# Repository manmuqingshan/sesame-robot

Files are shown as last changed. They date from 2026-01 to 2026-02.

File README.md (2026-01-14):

# The Sesame Robot Project 
___







sesame-cover

___

**Greetings, from your new best friend.**

Sesame is an accessible Open-Source robotics project based on the ESP32 microcontroller system, with an emphasis on expression and movement. 
This project is designed for makers and engineers of all skill levels! Sesame offers a dynamic platform designed to start working with walking robots. 
To build a sesame robot, you will need basic soldering skills, $50-60 in hardware components, access to a 3D printer, and a basic understanding of Arduino IDE.

This repository contains the CAD design files, STL files, build and wiring guides, and the base/expanded firmware for the ESP32-based controller. 
There is also some included debugging firmware that may be helpful in getting your Sesame up and running.

## Features

*   **Quadruped Design:** Uses 8 servo motors (2 per leg) to achieve roughly 8 total degrees of freedom.
*   **Emotive Display:** Features a 128x64 OLED screen acting as a reactive face that syncs with movement.
*   **Fully Printable:** Designed entirely for 3D printing in PLA with minimal supports.
*   **Sesame Studio:** New animation composer software to easily create custom movements.
*   **Serial CLI:** Control the robot and trigger animations via a Serial Command Line Interface or the web UI.
*   **Pre-programmed Emotes:** Includes animations for Walking, Waving, Dancing, Pointing, Resting, and more.

## Watch the launch video on YouTube

<a href="https://www.youtube.com/watch?v=1UDsWkcQZhc">thumb-youtube</a>

## Getting Started

Follow these steps to build your own Sesame Robot:

### 1. Gather Parts 
Check the **[Bill of Materials (BOM)](hardware/bom/README.md)** for a complete list of required electronics and hardware.
*   Microcontroller: ESP32 S2 Mini
*   Actuators: 8x MG90 Servos
*   Power: 5V 3A source

### 2. Print Parts 
Download the STLs and follow the **[Printing Guide](hardware/printing/README.md)**.
*   Designed for PLA
*   Minimal supports required

### 3. Build & Wire 
Follow the **[Build Guide](docs/build-guide/README.md)** and **[Wiring Guide](docs/wiring-guide/README.md)** to assemble the frame and connect the electronics.

### 4. Flash Firmware 
Upload the code from the **[Firmware Directory](firmware/README.md)**.
*   Requires Arduino IDE
*   Configure WiFi AP settings

### 5. Create Animations 
Use **[Sesame Studio](software/sesame-studio/README.md)** to visually design poses and sequences for your robot.

---

## Software & Firmware

### Sesame Studio
Sesame Studio is a standalone desktop application included in `software/sesame-studio/`. It allows you to:
*   Visually pose the robot using a schematic interface.
*   Generate C++ code for servo angles automatically.
*   Sequence frames into complex animations.

[**> Go to Sesame Studio**](software/sesame-studio/README.md)

sesamestudio-preview

### Firmware
The ESP32 firmware handles the kinematics, face display, and WiFi control interface.
*   **Web UI:** Control the robot from your phone via the built-in Access Point.
*   **Custom Faces:** Add your own bitmaps (guide in firmware docs).

[**> Go to Firmware Docs**](firmware/README.md)

firmware-preview

---

## Contributing

This robot is a platform for building new features, cosmetics, tools, and ideas. Since the current firmware is a basic implementation, pull requests are very welcome for:
*   Kinematics improvements
*   New animations
*   Improved Web UI/UX
*   Sensor integration (Ultrasonic, Gyro, etc.)

I would also love to see forks of this project with new hardware, software, faces, etc. Be sure to send me a message if you end up building one, and I might feature you on my website or channel!
  
sesame-army

---

*Created by [Dorian Todd](https://www.doriantodd.com/). Need help with your Sesame Robot? Send me a message on Discord, my username is "starphee"*

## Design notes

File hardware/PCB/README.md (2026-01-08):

# Schematics

Electronic schematics and wiring diagrams for the Sesame Robot.

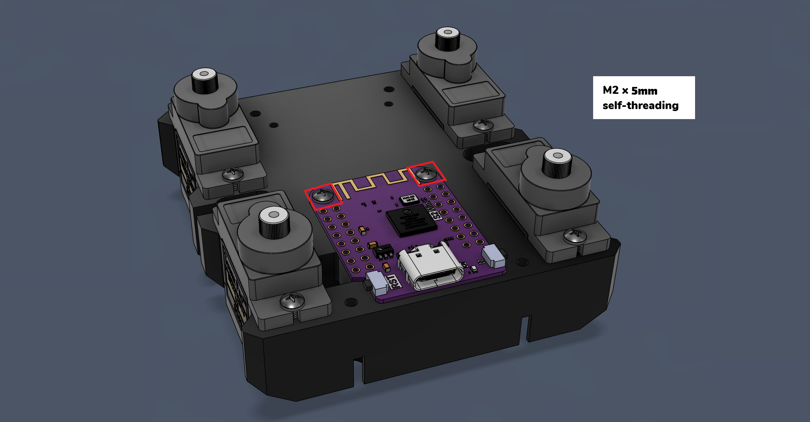
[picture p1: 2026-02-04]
docs/build-guide/assets/secure-electronics.png

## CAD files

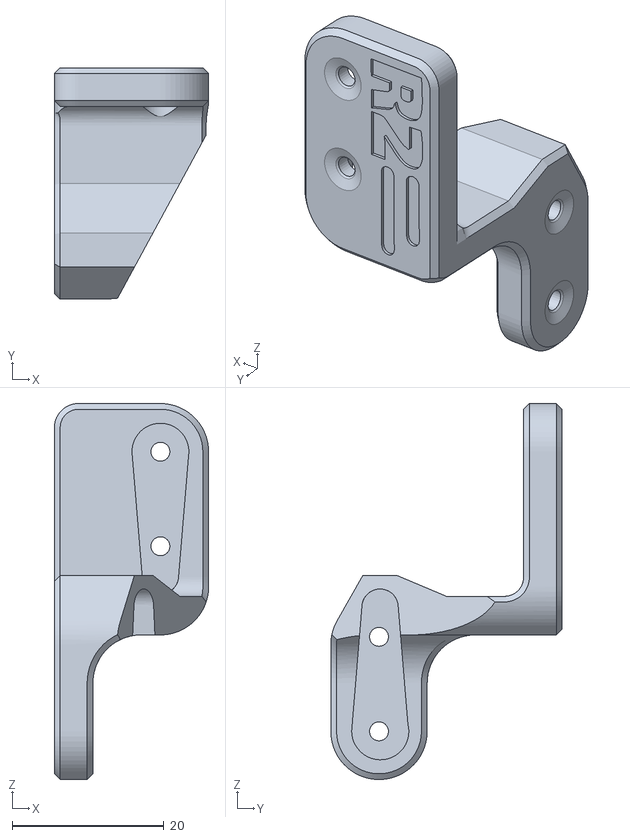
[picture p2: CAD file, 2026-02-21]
hardware/printing/stl/femurjoint-R2-v100.stl
20.3 x 30.5 x 49.5

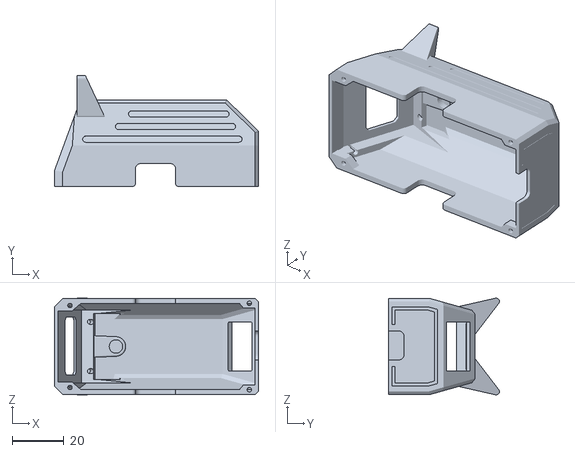
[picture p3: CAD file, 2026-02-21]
hardware/printing/stl/top-covers/Top-Cover-Cat-v100.stl
79.2 x 43.1 x 37.6

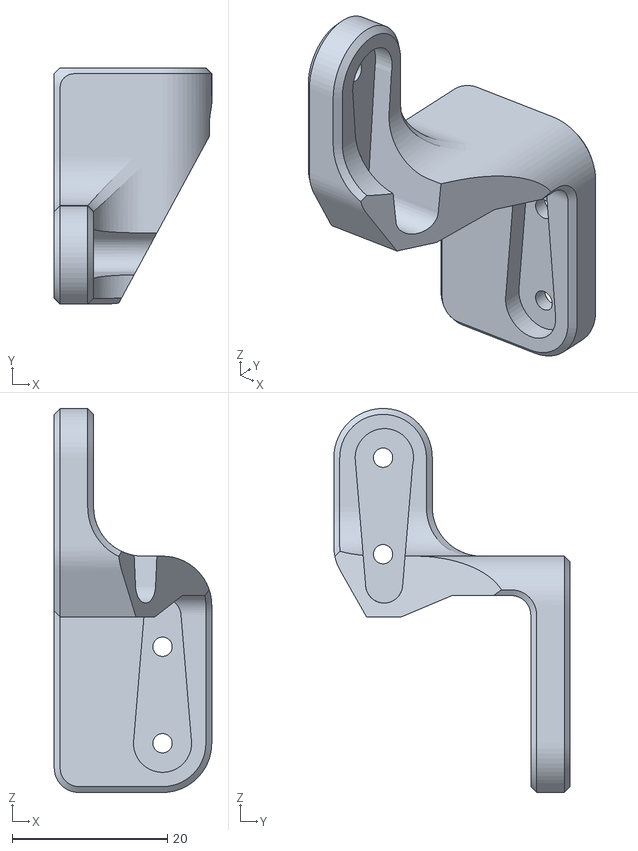
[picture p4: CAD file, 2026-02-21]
hardware/printing/stl/femurjoint-L2-v100.stl
20.3 x 30.5 x 49.5

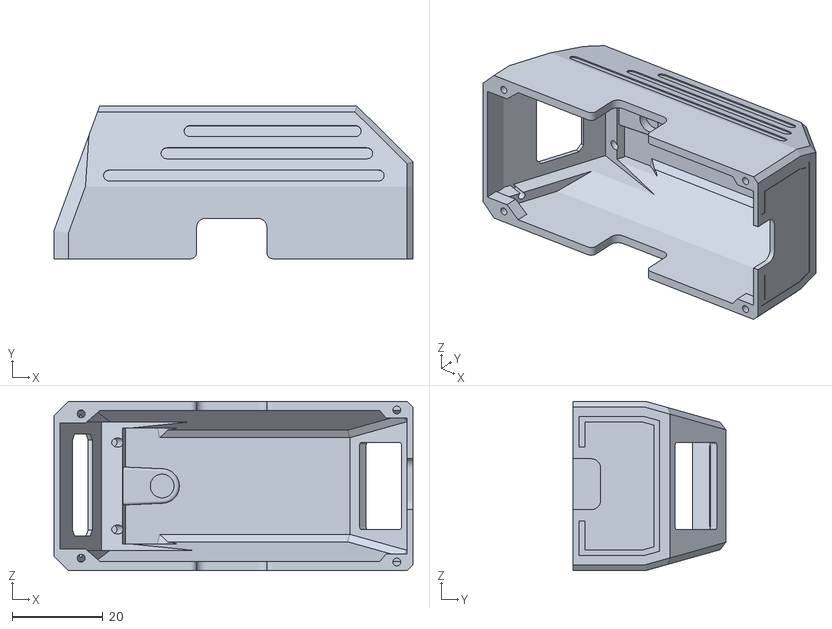
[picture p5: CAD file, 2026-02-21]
hardware/printing/stl/top-covers/Top-Cover-No-Ears-v100.stl
79.2 x 33.7 x 37.4

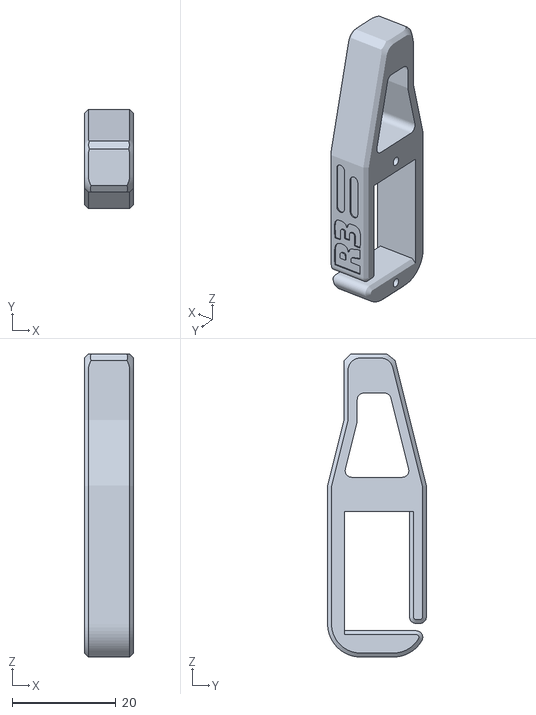
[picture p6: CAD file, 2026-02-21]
hardware/printing/stl/foot-joint-R3-v100.stl
9.53 x 19.0 x 58.4

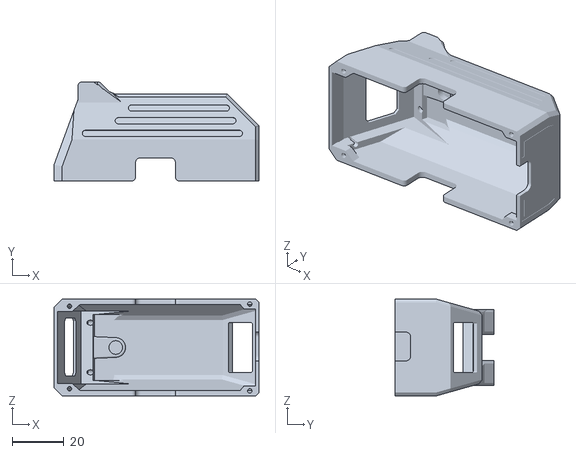
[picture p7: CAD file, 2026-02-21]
hardware/printing/stl/top-covers/Top-Cover-Enclosed-v100.stl
79.2 x 38.2 x 37.4

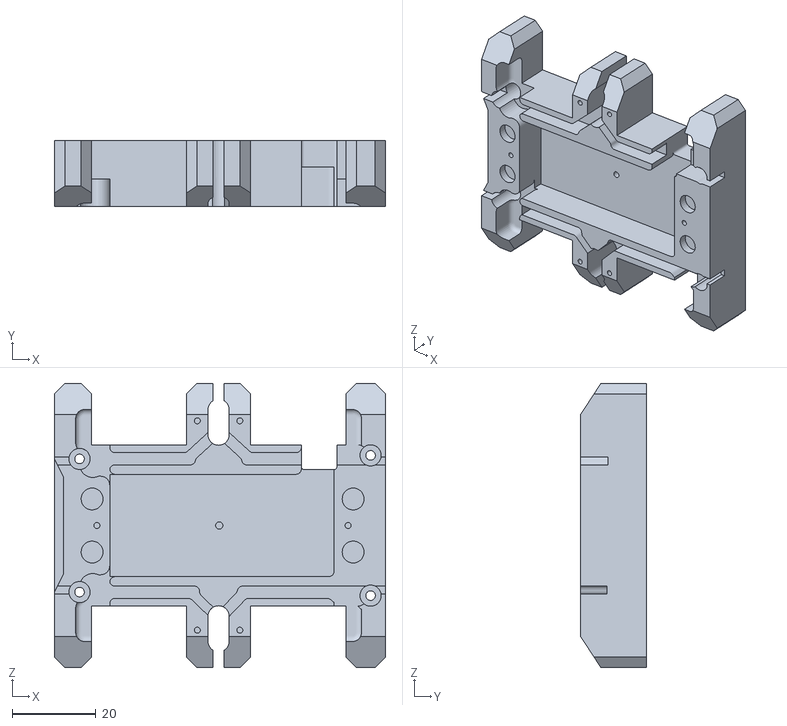
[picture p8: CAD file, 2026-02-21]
hardware/printing/stl/internal-frame-v100.stl
79.2 x 15.7 x 68.1

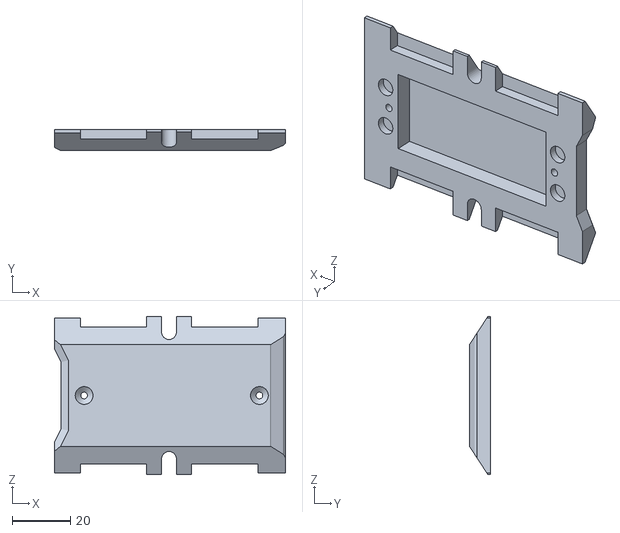
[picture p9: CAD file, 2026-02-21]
hardware/printing/stl/bottom-cover-v100.stl
79.2 x 7.27 x 54.2

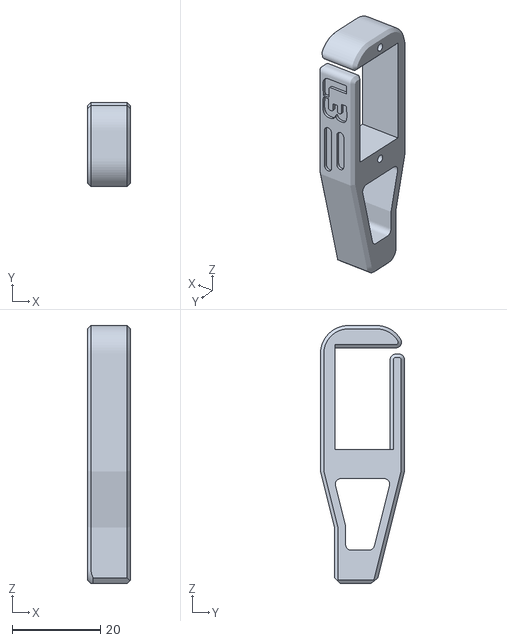
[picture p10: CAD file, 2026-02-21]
hardware/printing/stl/foot-joint-L3-v100.stl
9.70 x 19.0 x 58.4

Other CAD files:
hardware/printing/stl/femurjoint-R1-v100.stl
hardware/printing/stl/femurjoint-L1-v100.stl
hardware/printing/stl/foot-joint-R4-v100.stl
hardware/printing/stl/foot-joint-L4-v100.stl

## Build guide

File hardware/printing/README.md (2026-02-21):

# 3D Printing Guide

Sesame is designed to be printed in **PLA**. Most parts print without supports, but the top cover needs supports in targeted areas. Below is a quick reference for each component:

Note: There are 3 different top cover styles currently available. **Enclosed v91 is recommended** as it's the most modern design with magnetic hat mounts, covered display wires, and multicolor detail support. See [Top Covers](stl/top-covers/) for details on all styles.

## Recommended Settings
* **Material:** PLA / PLA+
* **Infill:** 8-10%
* **Wall Loops:** 2
* **Infill Pattern:** Honeycomb

## 3D Printed Components Support Guide

| Component | Supports Required | STL Link |
|---|---|---|
| Joint R1 | No | [femurjoint-R1-v100.stl](stl/femurjoint-R1-v100.stl) |
| Joint R2 | No | [femurjoint-R2-v100.stl](stl/femurjoint-R2-v100.stl) |
| Joint R3 | No | [foot-joint-R3-v100.stl](stl/foot-joint-R3-v100.stl) |
| Joint R4 | No | [foot-joint-R4-v100.stl](stl/foot-joint-R4-v100.stl) |
| Joint L1 | No | [femurjoint-L1-v100.stl](stl/femurjoint-L1-v100.stl) |
| Joint L2 | No | [femurjoint-L2-v100.stl](stl/femurjoint-L2-v100.stl) |
| Joint L3 | No | [foot-joint-L3-v100.stl](stl/foot-joint-L3-v100.stl) |
| Joint L4 | No | [foot-joint-L4-v100.stl](stl/foot-joint-L4-v100.stl) |
| Internal Frame  | No | [internal-frame-v100.stl](stl/internal-frame-v100.stl) |
| Bottom Cover | No | [bottom-cover-v100.stl](stl/bottom-cover-v100.stl) |
| Top Cover | Yes | [Top Covers](stl/top-covers/) |

### Top Cover Settings (Original Style)

Brim: Outer brim only
Support type: Normal (Manual)

Manual support locations:

topcover-supports2

This is what the part should look like sliced:

sliced-topcover

### Recommended Print Orientation for Joints:

Using the auto orientate tool will place these the correct way. 

sliced-topcover

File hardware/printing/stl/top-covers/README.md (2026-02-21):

# Top Cover Styles

## Enclosed v100
Current modern version of sesame top cover, includes 5mm x 2mm magnet slots for hats! Front display wires are covered, supports multicolor details.

## Cat v100
Modern Version of the enclosed top cover with cat ears instead of stubby ears! Updated with all current features with magnet support for hats, and multicolor details.

## No Ears v100
Template for designing your own ears for Sesame. The areas right next to where the ears ussually go is a little thin so this version is only really meant for desiging ears onto. (Includes all previously mentioned features)

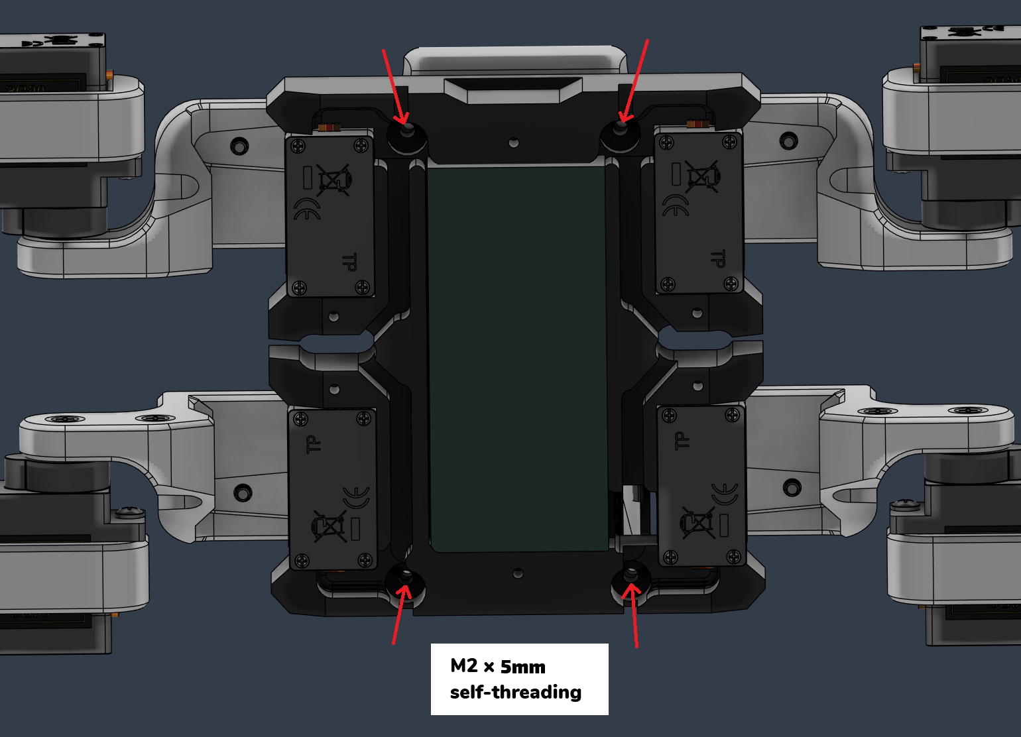
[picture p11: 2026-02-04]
docs/build-guide/assets/secure-top-cover.png

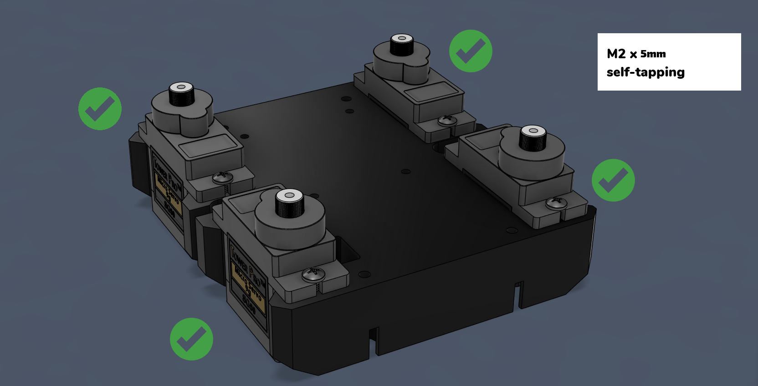
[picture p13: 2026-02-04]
docs/build-guide/assets/install-frame-motors.png

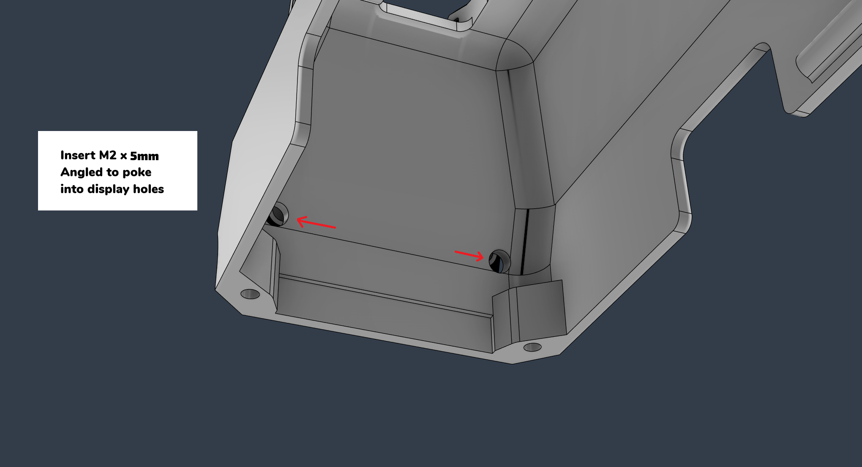
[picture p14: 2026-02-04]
docs/build-guide/assets/securing-display.png

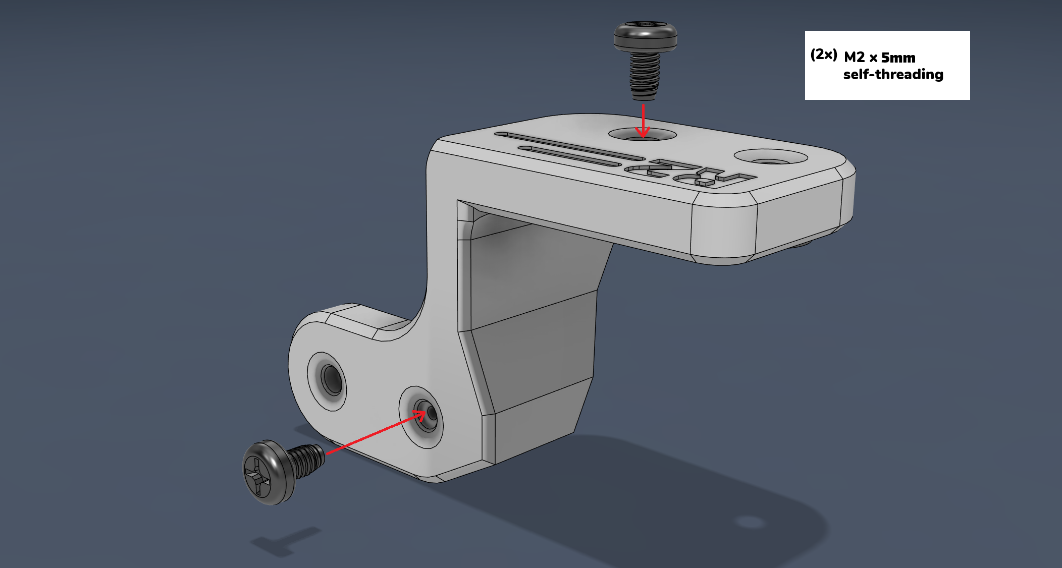
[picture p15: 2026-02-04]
docs/build-guide/assets/joint-horn-install-2.png

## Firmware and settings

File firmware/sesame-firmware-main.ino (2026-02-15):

#include <WiFi.h>
#include <WebServer.h>
#include <DNSServer.h>
#include <ESPmDNS.h>
#include <Wire.h>
#include <ESP32Servo.h>
#include <Adafruit_GFX.h>
#include <Adafruit_SSD1306.h>
#include "face-bitmaps.h"
#include "movement-sequences.h"
#include "captive-portal.h"

// --- Access Point Configuration ---
// This is the network the Robot will create
#define AP_SSID  "Sesame-Controller-BETA"
#define AP_PASS  "12345678" // Must be at least 8 characters

// --- Station Mode Configuration (Optional) ---
// Set these to connect to your home/office WiFi network
// Leave NETWORK_SSID empty to disable station mode
#define NETWORK_SSID ""  // Your WiFi network name
#define NETWORK_PASS ""  // Your WiFi password
#define ENABLE_NETWORK_MODE false  // Set to true to enable network connection attempts

#define SCREEN_WIDTH 128
#define SCREEN_HEIGHT 64
#define OLED_RESET -1
#define OLED_I2C_ADDR 0x3C

// I2C Pins for Distro Board V2
//#define I2C_SDA 8
//#define I2C_SCL 9

// I2C Pins for Distro Board
//#define I2C_SDA 21
//#define I2C_SCL 22

// I2C Pins for S2 Mini Board
#define I2C_SDA 33
#define I2C_SCL 35


// DNS Server for Captive Portal
DNSServer dnsServer;
const byte DNS_PORT = 53;

Adafruit_SSD1306 display(SCREEN_WIDTH, SCREEN_HEIGHT, &Wire, OLED_RESET);
WebServer server(80);

// Global state for animations
String currentCommand = "";
String currentFaceName = "default";
const unsigned char* const* currentFaceFrames = nullptr;
uint8_t currentFaceFrameCount = 0;
uint8_t currentFaceFrameIndex = 0;
unsigned long lastFaceFrameMs = 0;
int faceFps = 8;
FaceAnimMode currentFaceMode = FACE_ANIM_LOOP;
int8_t faceFrameDirection = 1;
bool faceAnimFinished = false;
int currentFaceFps = 0;
bool idleActive = false;
bool idleBlinkActive = false;
unsigned long nextIdleBlinkMs = 0;
uint8_t idleBlinkRepeatsLeft = 0;

// WiFi Info Scrolling
unsigned long lastInputTime = 0;
bool firstInputReceived = false;
bool showingWifiInfo = false;
int wifiScrollPos = 0;
unsigned long lastWifiScrollMs = 0;
String wifiInfoText = "";

// Network Mode
bool networkConnected = false;
IPAddress networkIP;
String deviceHostname = "sesame-robot";

// Servo Pins for Distro Board
// ======================================================================
// Pin numbers are coorisponding to the ESP32 GPIO pins and may differ based on which board you use.
// If you are using a different board, please adjust the servoPins array accordingly.
// ======================================================================
Servo servos[8];
// Sesame Distro Board V2 Pinout
//const int servoPins[8] = {4, 5, 6, 7, 15, 16, 17, 18};

// Sesame Distro Board Pinout
//const int servoPins[8] = {15, 2, 23, 19, 4, 16, 17, 18};

// Lolin S2 Mini Pinout
const int servoPins[8] = {1, 2, 4, 6, 8, 10, 13, 14};

// Subtrim values for each servo (offset in degrees)
int8_t servoSubtrim[8] = {0, 0, 0, 0, 0, 0, 0, 0};


// Animation constants
int frameDelay = 100;
int walkCycles = 10;
int motorCurrentDelay = 20; // ms delay between motor movements to prevent over-current

struct FaceEntry {
  const char* name;
  const unsigned char* const* frames;
  uint8_t maxFrames;
};

static const uint8_t MAX_FACE_FRAMES = 6;

#define MAKE_FACE_FRAMES(name) \
  const unsigned char* const face_##name##_frames[] = { \
    epd_bitmap_##name, epd_bitmap_##name##_1, epd_bitmap_##name##_2, \
    epd_bitmap_##name##_3, epd_bitmap_##name##_4, epd_bitmap_##name##_5 \
  };

#define X(name) MAKE_FACE_FRAMES(name)
FACE_LIST
#undef X
#undef MAKE_FACE_FRAMES

const FaceEntry faceEntries[] = {
#define X(name) { #name, face_##name##_frames, MAX_FACE_FRAMES },
  FACE_LIST
#undef X
  { "default", face_defualt_frames, MAX_FACE_FRAMES }
};

struct FaceFpsEntry {
  const char* name;
  uint8_t fps;
};

const FaceFpsEntry faceFpsEntries[] = {
  { "walk", 1 },
  { "rest", 1 },
  { "swim", 1 },
  { "dance", 1 },
  { "wave", 1 },
  { "point", 5 },
  { "stand", 1 },
  { "cute", 1 },
  { "pushup", 1 },
  { "freaky", 1 },
  { "bow", 1 },
  { "worm", 1 },
  { "shake", 1 },
  { "shrug", 1 },
  { "dead", 2 },
  { "crab", 1 },
  { "idle", 1 },
  { "idle_blink", 7 },
  { "default", 1 },
  // Conversational faces (manually controlled by Python - no auto-animation)
  { "happy", 1 },
  { "talk_happy", 1 },
  { "sad", 1 },
  { "talk_sad", 1 },
  { "angry", 1 },
  { "talk_angry", 1 },
  { "surprised", 1 },
  { "talk_surprised", 1 },
  { "sleepy", 1 },
  { "talk_sleepy", 1 },
  { "love", 1 },
  { "talk_love", 1 },
  { "excited", 1 },
  { "talk_excited", 1 },
  { "confused", 1 },
  { "talk_confused", 1 },
  { "thinking", 1 },
  { "talk_thinking", 1 },
};


// Prototypes
void setServoAngle(uint8_t channel, int angle);
void updateFaceBitmap(const unsigned char* bitmap);
void setFace(const String& faceName);
void setFaceMode(FaceAnimMode mode);
void setFaceWithMode(const String& faceName, FaceAnimMode mode);
void updateAnimatedFace();
void delayWithFace(unsigned long ms);
void enterIdle();
void exitIdle();
void updateIdleBlink();
int getFaceFpsForName(const String& faceName);
bool pressingCheck(String cmd, int ms);
void handleGetSettings();
void handleSetSettings();
void handleGetStatus();
void handleApiCommand();
void updateWifiInfoScroll();
void recordInput();

void handleRoot() {
  server.send(200, "text/html", index_html);
}

void handleCommandWeb() {
  // We send 200 OK immediately so the web browser doesn't hang waiting for animation to finish
  if (server.hasArg("pose")) {
    currentCommand = server.arg("pose");
    recordInput();
    exitIdle();
    server.send(200, "text/plain", "OK"); 
  } 
  else if (server.hasArg("go")) {
    currentCommand = server.arg("go");
    recordInput();
    exitIdle();
    server.send(200, "text/plain", "OK");
  } 
  else if (server.hasArg("stop")) {
    currentCommand = "";
    recordInput();
    server.send(200, "text/plain", "OK");
  }
  else if (server.hasArg("motor") && server.hasArg("value")) {
    int motorNum = server.arg("motor").toInt();
    int servoIdx = servoNameToIndex(server.arg("motor"));
    int angle = server.arg("value").toInt();
    if (motorNum >= 1 && motorNum <= 8 && angle >= 0 && angle <= 180) {
      setServoAngle(motorNum - 1, angle); // Convert 1-based to 0-based index
      recordInput();
      server.send(200, "text/plain", "OK");
    } else if (servoIdx != -1 && angle >= 0 && angle <= 180) {
      setServoAngle(servoIdx, angle);
      recordInput();
      server.send(200, "text/plain", "OK");
    } else {
      server.send(400, "text/plain", "Invalid motor or angle");
    }
  }
  else {
    server.send(400, "text/plain", "Bad Args");
  }
}

void handleGetSettings() {
  String json = "{";
  json += "\"frameDelay\":" + String(frameDelay) + ",";
  json += "\"walkCycles\":" + String(walkCycles) + ",";
  json += "\"motorCurrentDelay\":" + String(motorCurrentDelay) + ",";
  json += "\"faceFps\":" + String(faceFps);
  json += "}";
  server.send(200, "application/json", json);
}

void handleSetSettings() {
  if (server.hasArg("frameDelay")) frameDelay = server.arg("frameDelay").toInt();
  if (server.hasArg("walkCycles")) walkCycles = server.arg("walkCycles").toInt();
  if (server.hasArg("motorCurrentDelay")) motorCurrentDelay = server.arg("motorCurrentDelay").toInt();
  if (server.hasArg("faceFps")) faceFps = (int)max(1L, server.arg("faceFps").toInt());
  server.send(200, "text/plain", "OK");
}

// API endpoint for network clients to get robot status
void handleGetStatus() {
  String json = "{";
  json += "\"currentCommand\":\"" + currentCommand + "\",";
  json += "\"currentFace\":\"" + currentFaceName + "\",";
  json += "\"networkConnected\":" + String(networkConnected ? "true" : "false") + ",";
  json += "\"apIP\":\"" + WiFi.softAPIP().toString() + "\"";
  if (networkConnected) {
    json += ",\"networkIP\":\"" + networkIP.toString() + "\"";
  }
  json += "}";
  server.send(200, "application/json", json);
}

// API endpoint for network clients to send commands (JSON-based)
void handleApiCommand() {
  if (server.method() != HTTP_POST) {
    server.send(405, "application/json", "{\"error\":\"Method not allowed\"}");
    return;
  }
  
  String body = server.arg("plain");
  
  Serial.println("API Command received:");
  Serial.println(body);
  
  // Check for face-only command (no movement)
  int faceOnlyStart = body.indexOf("\"face\":\"");
  if (faceOnlyStart == -1) {
    faceOnlyStart = body.indexOf("\"face\": \"");
  }
  
  // If we have a face but no command field, it's face-only
  bool faceOnly = (faceOnlyStart > 0 && body.indexOf("\"command\":") == -1 && body.indexOf("\"command\": ") == -1);
  
  String command = "";
  String face = "";
  
  // Parse face
  if (faceOnlyStart > 0) {
    faceOnlyStart = body.indexOf("\"", faceOnlyStart + 6) + 1;
    int faceEnd = body.indexOf("\"", faceOnlyStart);
    if (faceEnd > faceOnlyStart) {
      face = body.substring(faceOnlyStart, faceEnd);
      Serial.print("Parsed face: ");
      Serial.println(face);
    }
  }
  
  // Parse command (if not face-only)
  if (!faceOnly) {
    int cmdStart = body.indexOf("\"command\":\"");
    if (cmdStart == -1) {
      cmdStart = body.indexOf("\"command\": \"");
    }
    
    if (cmdStart == -1) {
      Serial.println("Error: command field not found");
      server.send(400, "application/json", "{\"error\":\"Missing command field\"}");
      return;
    }
    
    cmdStart = body.indexOf("\"", cmdStart + 10) + 1;
    int cmdEnd = body.indexOf("\"", cmdStart);
    
    if (cmdEnd <= cmdStart) {
      Serial.println("Error: invalid command format");
      server.send(400, "application/json", "{\"error\":\"Invalid command format\"}");
      return;
    }
    
    command = body.substring(cmdStart, cmdEnd);
    Serial.print("Parsed command: ");
    Serial.println(command);
  }
  
  // Set face if provided
  if (face.length() > 0) {
    setFace(face);
  }
  
  // If face-only, just acknowledge
  if (faceOnly) {
    recordInput();
    server.send(200, "application/json", "{\"status\":\"ok\",\"message\":\"Face updated\"}");
    return;
  }
  
  // Execute command
  if (command == "stop") {
    currentCommand = "";
    recordInput();
    server.send(200, "application/json", "{\"status\":\"ok\",\"message\":\"Command stopped\"}");
  } else {
    currentCommand = command;
    recordInput();
    exitIdle();
    server.send(200, "application/json", "{\"status\":\"ok\",\"message\":\"Command executed\"}");
  }
}

void setup() {
  Serial.begin(115200);
  randomSeed(micros());
  
  // I2C Init for ESP32
  Wire.begin(I2C_SDA, I2C_SCL);

  // OLED Init
  if (!display.begin(SSD1306_SWITCHCAPVCC, OLED_I2C_ADDR)) {
    Serial.println(F("SSD1306 allocation failed."));
    while (1);
  }
  
  display.clearDisplay();
  display.setTextColor(SSD1306_WHITE);
  display.setTextSize(1);
  display.setCursor(0,0);
  display.println(F("Setting up WiFi..."));
  display.display();

  // --- WIFI CONFIGURATION ---
  // Try to connect to network first if configured
  if (ENABLE_NETWORK_MODE && String(NETWORK_SSID).length() > 0) {
    Serial.println("Attempting to connect to network: " + String(NETWORK_SSID));
    WiFi.mode(WIFI_AP_STA); // Enable both AP and Station modes
    WiFi.setHostname(deviceHostname.c_str());
    WiFi.begin(NETWORK_SSID, NETWORK_PASS);
    
    // Wait up to 10 seconds for connection
    int attempts = 0;
    while (WiFi.status() != WL_CONNECTED && attempts < 20) {
      delay(500);
      Serial.print(".");
      attempts++;
    }
    
    if (WiFi.status() == WL_CONNECTED) {
      networkConnected = true;
      networkIP = WiFi.localIP();
      Serial.println();
      Serial.print("Connected to network! IP: ");
      Serial.println(networkIP);
    } else {
      Serial.println();
      Serial.println("Failed to connect to network. Running in AP-only mode.");
      WiFi.mode(WIFI_AP); // Fall back to AP-only
    }
  } else {
    WiFi.mode(WIFI_AP);
    Serial.println("Network mode disabled. Running in AP-only mode.");
  }
  
  // --- ACCESS POINT CONFIGURATION ---
  WiFi.softAP(AP_SSID, AP_PASS);
  IPAddress myIP = WiFi.softAPIP();
  
  Serial.print("AP Created. IP: ");
  Serial.println(myIP);

  // Build WiFi info text for scrolling
  if (networkConnected) {
    wifiInfoText = "AP: " + String(AP_SSID) + " (" + myIP.toString() + ")  |  Network: " + String(NETWORK_SSID) + " (" + networkIP.toString() + ") or " + deviceHostname + ".local  |  ";
  } else {
    wifiInfoText = "Connect to WiFi: " + String(AP_SSID) + "  |  Pass: " + String(AP_PASS) + "  |  IP: " + myIP.toString() + "  |  Captive Portal will auto-open!  |  ";
  }
  
  // Initialize input tracking
  lastInputTime = millis();
  firstInputReceived = false;
  showingWifiInfo = false;

  // Start mDNS responder for local network discovery
  if (MDNS.begin(deviceHostname.c_str())) {
    Serial.println("mDNS responder started");
    Serial.print("Access controller at: http://");
    Serial.print(deviceHostname);
    Serial.println(".local");
    MDNS.addService("http", "tcp", 80);
  } else {
    Serial.println("Error setting up mDNS responder!");
  }

  // Start DNS Server for Captive Portal
  // This redirects ALL domain requests to the ESP32's IP
  dnsServer.start(DNS_PORT, "*", myIP);

  // Web Server Routes
  server.on("/", handleRoot);
  server.on("/cmd", handleCommandWeb);
  server.on("/getSettings", handleGetSettings);
  server.on("/setSettings", handleSetSettings);
  
  // API endpoints for network communication
  server.on("/api/status", handleGetStatus);
  server.on("/api/command", handleApiCommand);
  
  // Catch-all route for captive portal
  // This ensures any URL redirects to the controller page
  server.onNotFound(handleRoot);
  
  server.begin();

  // PWM Init
  ESP32PWM::allocateTimer(0);
  ESP32PWM::allocateTimer(1);
  ESP32PWM::allocateTimer(2);
  ESP32PWM::allocateTimer(3);
  
  for (int i = 0; i < 8; i++) {
    servos[i].setPeriodHertz(50);
    // Map 0-180 to approx 732-2929us
    servos[i].attach(servoPins[i], 732, 2929);
  }
  delay(10);
  
  // Show rest face on startup without moving motors
  setFace("rest");
  
  Serial.println(F("HTTP server & Captive Portal started."));
}

void loop() {
  // Process DNS requests for captive portal
  dnsServer.processNextRequest();
  
  server.handleClient();
  updateAnimatedFace();
  updateIdleBlink();
  updateWifiInfoScroll();

  if (currentCommand != "") {
    String cmd = currentCommand;
    if (cmd == "forward") runWalkPose();
    else if (cmd == "backward") runWalkBackward();
    else if (cmd == "left") runTurnLeft();
    else if (cmd == "right") runTurnRight();
    else if (cmd == "rest") { runRestPose(); if (currentCommand == "rest") currentCommand = ""; }
    else if (cmd == "stand") { runStandPose(1); if (currentCommand == "stand") currentCommand = ""; }
    else if (cmd == "wave") runWavePose();
    else if (cmd == "dance") runDancePose();
    else if (cmd == "swim") runSwimPose();
    else if (cmd == "point") runPointPose();
    else if (cmd == "pushup") runPushupPose();
    else if (cmd == "bow") runBowPose();
    else if (cmd == "cute") runCutePose();
    else if (cmd == "freaky") runFreakyPose();
    else if (cmd == "worm") runWormPose();
    else if (cmd == "shake") runShakePose();
    else if (cmd == "shrug") runShrugPose();
    else if (cmd == "dead") runDeadPose();
    else if (cmd == "crab") runCrabPose();
  }
  
  // Serial CLI for debugging (can be used to diagnose servo position issues and wiring)
  if (Serial.available()) {
    static char command_buffer[32];
    static byte buffer_pos = 0;
    char c = Serial.read();
    if (c == '\n' || c == '\r') {
      if (buffer_pos > 0) {
        command_buffer[buffer_pos] = '\0';
        int motorNum, angle;
        recordInput();
        if(strcmp(command_buffer, "run walk") == 0 || strcmp(command_buffer, "rn wf") == 0) { currentCommand = "forward"; runWalkPose(); currentCommand = ""; }
        else if(strcmp(command_buffer, "rn wb") == 0) { currentCommand = "backward"; runWalkBackward(); currentCommand = ""; }
        else if(strcmp(command_buffer, "rn tl") == 0) { currentCommand = "left"; runTurnLeft(); currentCommand = ""; }
        else if(strcmp(command_buffer, "rn tr") == 0) { currentCommand = "right"; runTurnRight(); currentCommand = ""; }
        else if(strcmp(command_buffer, "run rest") == 0 || strcmp(command_buffer, "rn rs") == 0) runRestPose();
        else if(strcmp(command_buffer, "run stand") == 0 || strcmp(command_buffer, "rn st") == 0) runStandPose(1);
        else if(strcmp(command_buffer, "rn wv") == 0) { currentCommand = "wave"; runWavePose(); }
        else if(strcmp(command_buffer, "rn dn") == 0) { currentCommand = "dance"; runDancePose(); }
        else if(strcmp(command_buffer, "rn sw") == 0) { currentCommand = "swim"; runSwimPose(); }
        else if(strcmp(command_buffer, "rn pt") == 0) { currentCommand = "point"; runPointPose(); }
        else if(strcmp(command_buffer, "rn pu") == 0) { currentCommand = "pushup"; runPushupPose(); }
        else if(strcmp(command_buffer, "rn bw") == 0) { currentCommand = "bow"; runBowPose(); }
        else if(strcmp(command_buffer, "rn ct") == 0) { currentCommand = "cute"; runCutePose(); }
        else if(strcmp(command_buffer, "rn fk") == 0) { currentCommand = "freaky"; runFreakyPose(); }
        else if(strcmp(command_buffer, "rn wm") == 0) { currentCommand = "worm"; runWormPose(); }
        else if(strcmp(command_buffer, "rn sk") == 0) { currentCommand = "shake"; runShakePose(); }
        else if(strcmp(command_buffer, "rn sg") == 0) { currentCommand = "shrug"; runShrugPose(); }
        else if(strcmp(command_buffer, "rn dd") == 0) { currentCommand = "dead"; runDeadPose(); }
        else if(strcmp(command_buffer, "rn cb") == 0) { currentCommand = "crab"; runCrabPose(); }
        else if (strcmp(command_buffer, "subtrim") == 0 || strcmp(command_buffer, "st") == 0) {
          Serial.println("Subtrim values:");
          for (int i = 0; i < 8; i++) {
            Serial.print("Motor "); Serial.print(i); Serial.print(": ");
            if (servoSubtrim[i] >= 0) Serial.print("+");
            Serial.println(servoSubtrim[i]);
          }
        }
        else if (strcmp(command_buffer, "subtrim save") == 0 || strcmp(command_buffer, "st save") == 0) {
          Serial.println("Copy and paste this into your code:");
          Serial.print("int8_t servoSubtrim[8] = {");
          for (int i = 0; i < 8; i++) {
            Serial.print(servoSubtrim[i]);
            if (i < 7) Serial.print(", ");
          }
          Serial.println("};");
        }
        else if (strncmp(command_buffer, "subtrim reset", 13) == 0 || strncmp(command_buffer, "st reset", 8) == 0) {
          for (int i = 0; i < 8; i++) servoSubtrim[i] = 0;
          Serial.println("All subtrim values reset to 0");
        }
        else if (strncmp(command_buffer, "subtrim ", 8) == 0 || strncmp(command_buffer, "st ", 3) == 0) {
          const char* params = (command_buffer[1] == 't') ? command_buffer + 3 : command_buffer + 8;
          int trimMotor, trimValue;
          if (sscanf(params, "%d %d", &trimMotor, &trimValue) == 2) {
            if (trimMotor >= 0 && trimMotor < 8) {
              if (trimValue >= -90 && trimValue <= 90) {
                servoSubtrim[trimMotor] = trimValue;
                Serial.print("Motor "); Serial.print(trimMotor); Serial.print(" subtrim set to ");
                if (trimValue >= 0) Serial.print("+");
                Serial.println(trimValue);
              } else {
                Serial.println("Subtrim value must be between -90 and +90");
              }
            } else {
              Serial.println("Invalid motor number (0-7)");
            }
          }
        }
        else if (strncmp(command_buffer, "all ", 4) == 0) {
             if (sscanf(command_buffer + 4, "%d", &angle) == 1) {
                 for (int i = 0; i < 8; i++) setServoAngle(i, angle);
                 Serial.print("All servos set to "); Serial.println(angle);
             }
        }
        else if (sscanf(command_buffer, "%d %d", &motorNum, &angle) == 2) {
             if (motorNum >= 0 && motorNum < 8) {
                 setServoAngle(motorNum, angle);
                 Serial.print("Servo "); Serial.print(motorNum); Serial.print(" set to "); Serial.println(angle);
             } else {
                 Serial.println("Invalid motor number (0-7)");
             }
        }
        buffer_pos = 0;
      }
    } else if (buffer_pos < sizeof(command_buffer) - 1) {
      command_buffer[buffer_pos++] = c;
    }
  }
}

// Function to update the robot's face
void updateFaceBitmap(const unsigned char* bitmap) {
  display.clearDisplay();
  display.drawBitmap(0, 0, bitmap, 128, 64, SSD1306_WHITE);
  display.display();
}

uint8_t countFrames(const unsigned char* const* frames, uint8_t maxFrames) {
  if (frames == nullptr || frames[0] == nullptr) return 0;
  uint8_t count = 0;
  for (uint8_t i = 0; i < maxFrames; i++) {
    if (frames[i] == nullptr) break;
    count++;
  }
  return count;
}
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

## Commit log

2026-01-08 Add README files for PCB, BOM, and 3D printing guides
    Added initial README.md files for hardware/PCB and hardware/printing directories, providing overviews for schematics and 3D printing instructions. Expanded hardware/bom/README.md with rough component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
2026-02-03 Update STL links to v90 in printing README
    Bump referenced STL files in hardware/printing/README.md to the v90 revisions and normalize several filenames. Updated entries for Joint R1-R4, Joint L1-L4, Internal Frame, and Bottom Cover to point 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
2026-02-04 Update Build Guide Photos
    Fix screw dimensions to normalized M2x5mm
2026-02-07 fix: typo in rocker power switch model number
    I believe the rocker switches are KCD1s
2026-02-18 Removed debug print not cleaned up in last PR
2026-02-19 fix(bom): make link destination explicit and rename column to Source
2026-02-21 Update all hardware to v100
    Update source hardware files, links and all stl print files to v100 revision.
    v100 hardware changes:
    Overall frame length has been increased by 0.25in to account for V2 distro board and wire sizing. Top cover ear revs have been migrated and updated. Various other changes including hole positioning a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
    [Top-Cover-Cat-v100.stl, Top-Cover-Enclosed-v100.stl, Top-Cover-No-Ears-v100.stl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]

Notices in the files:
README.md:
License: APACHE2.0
